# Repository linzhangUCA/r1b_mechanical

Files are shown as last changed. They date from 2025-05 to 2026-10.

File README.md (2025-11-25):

# R1Bot's Mechanical Design

## Preview
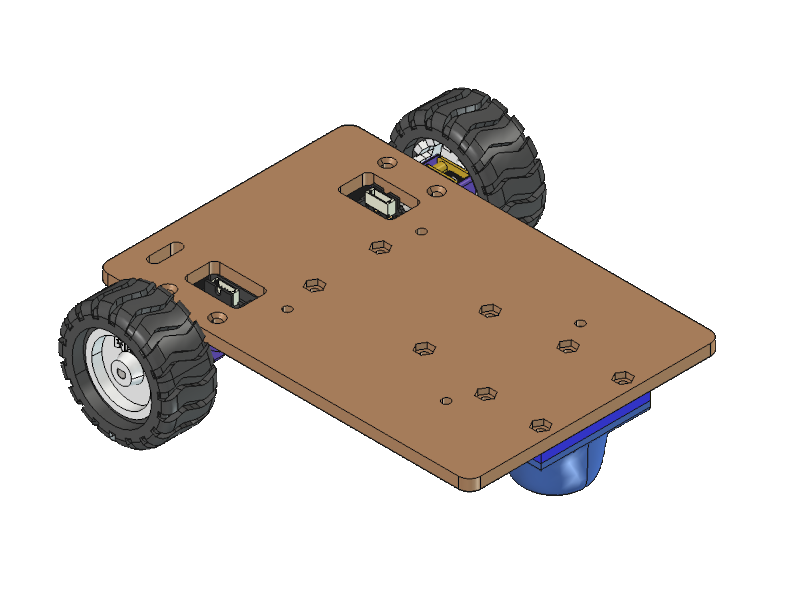
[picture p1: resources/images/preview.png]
preview


## Assembly Parts List
| Name | Description | Quantity |
| :--- | :--- | ---: |
| [Base plate](/prints/STL/Base.stl) | holds all components | 1 |
| [Motor Bracket](/prints/STL/MotorBracket.stl) | holds motor on base | 2 |
| [Caster Wheel](/prints/STL/CasterWheel.stl) | offers omni-directional rotate | 1 |
| M2.5x14 flathead screw | secures caster wheel on base  | 4 |
| [Tire](/prints/STL/Tire.stl) | provides traction | 2 |
| [Wheel](/prints/STL/Wheel.stl) | attaches to motor and supports tire | 2 |
| [N20 geared DC motor with encoder](https://www.robotshop.com/products/e-s-motor-6v-1001-micro-metal-gearmotor-w-encoder-cable-150rpm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) | spins and senses wheel | 2 |
| M2.5x8 flathead screw | secures motor bracket on base  | 4 |
| [Battery holder](https://a.co/d/j4Nehb4) | hosts 2 Li-ion batteries  | 1 |
| 18650 Lithium-ion Battery | provides DC power | 2 |
| M2.5x5 flathead screw | secures battery holder on base  | 4 |
| M2.5 nut | pairs with the screws  | 16 |
| [Power expansion board](https://category.yahboom.net/collections/rp-power/products/power-board-pi5) (PEB) | regulates 6~24 V to 5 V  | 1 |
| M2.5x10 standoff | supports PEB | 4 |
| [Motor control board](https://github.com/linzhangUCA/r1b_electrical) (MCB) | bridges Pico, Pololu713, HC-SR04, motors and encoders  | 1 |
| M2.5x15 standoff | supports MCB | 4 |
| M2.5x6 screw | caps MCB | 4 |

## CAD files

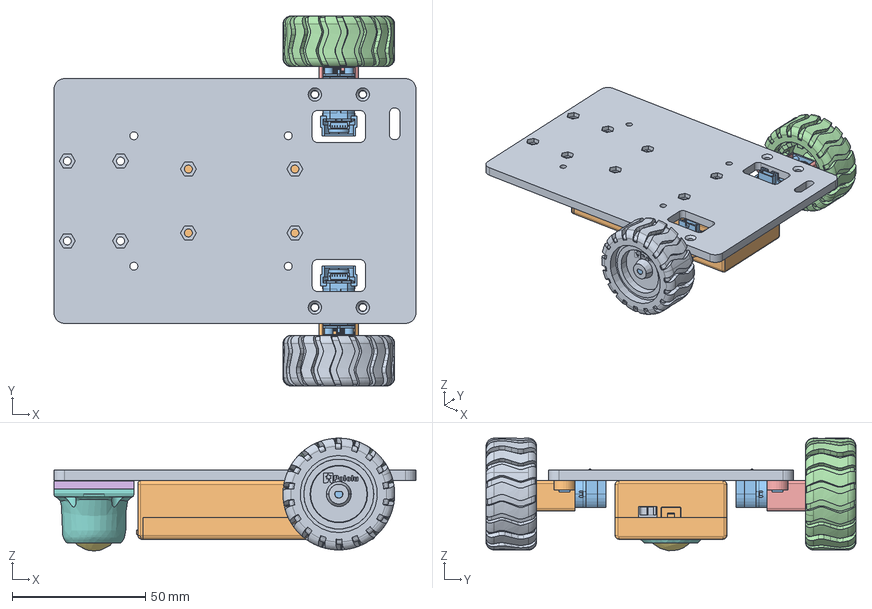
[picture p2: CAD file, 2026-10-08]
tbot_assembly.FCStd
136.0 x 139.0 x 42.3 mm
base_link
Case, 3.7V 2X 18650 Battery Holder with On Off Switch
Switch and Wiring Cover, 3.7V 2X 18650 Battery Holder with On Off Switch
Battery Conduction Clip, 3.7V 2X 18650 Battery Holder with On Off Switch
Spring, 3.7V 2X 18650 Battery Holder with On Off Switch
Battery Conduction Clip, Positive Terminal, 3.7V 2X 18650 Battery Holder with On Off Switch
Battery Conduction Clip, Negative Terminal, 3.7V 2X 18650 Battery Holder with On Off Switch
Spring, 3.7V 2X 18650 Battery Holder with On Off Switch001
Slide Switch SPDT, 3.7V 2X 18650 Battery Holder with On Off Switch_OFF
Cover, 3.7V 2X 18650 Battery Holder with On Off Switch
left_Pololu_motor
left_wheel
left_motor_backet
LiftPad
Roller_Sphere
Roller_Housing
right_wheel
right_motor_backet
right_Pololu_motor

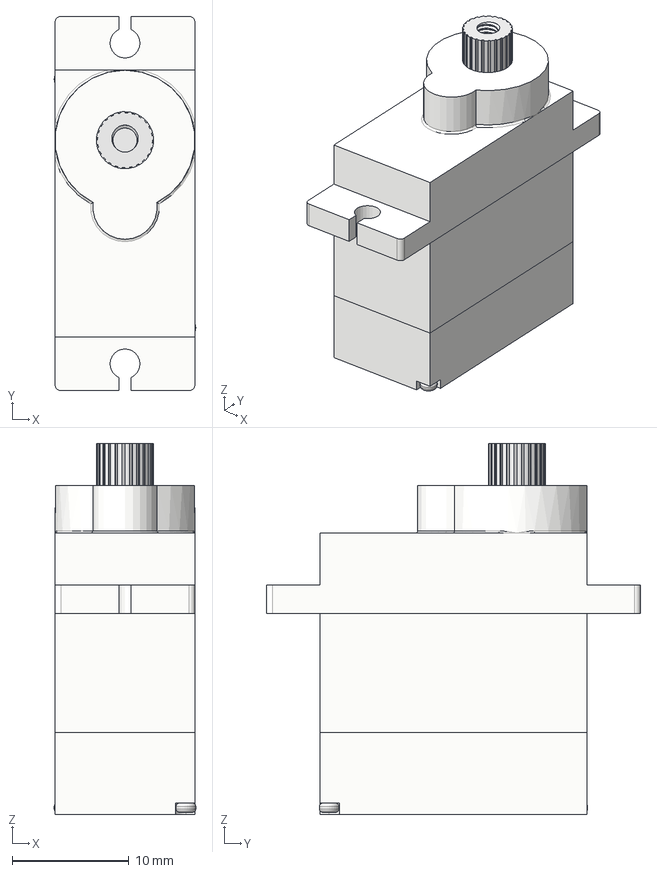
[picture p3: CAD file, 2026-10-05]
resources/steps/Assembly Micro Servo MG90S.step
12.1 x 32.1 x 31.8 mm
Micro Motor
Middel Part
Buttom Part
Shaft B
Gear C
Gear B
Gear A
Main Shaft with Gear
Upper Part
Main Screw x 2

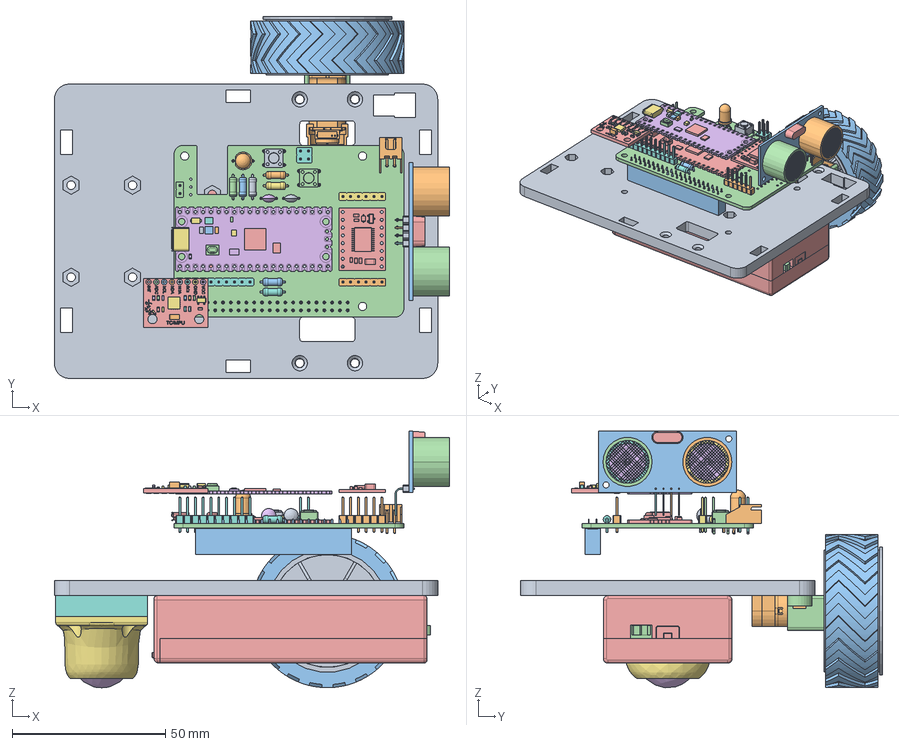
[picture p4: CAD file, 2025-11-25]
RobotAssembly.FCStd
128.9 x 118.0 x 83.6 mm
Wheel
Motor
Tire
MotorBacket
Case, 3.7V 2X 18650 Battery Holder with On Off Switch
Switch and Wiring Cover, 3.7V 2X 18650 Battery Holder with On Off Switch
Battery Conduction Clip, 3.7V 2X 18650 Battery Holder with On Off Switch
Spring, 3.7V 2X 18650 Battery Holder with On Off Switch
Battery Conduction Clip, Positive Terminal, 3.7V 2X 18650 Battery Holder with On Off Switch
Battery Conduction Clip, Negative Terminal, 3.7V 2X 18650 Battery Holder with On Off Switch
Spring, 3.7V 2X 18650 Battery Holder with On Off Switch001
Slide Switch SPDT, 3.7V 2X 18650 Battery Holder with On Off Switch_OFF
Cover, 3.7V 2X 18650 Battery Holder with On Off Switch
Roller_Sphere
Roller_Housing
LiftPad
Base
JST_XH_S2B-XH-A_1x02_P2.50mm_Horizontal
R_Axial_DIN0207_L6.3mm_D2.5mm_P7.62mm_Horizontal
R_Axial_DIN0207_L6.3mm_D2.5mm_P7.62mm_Horizontal001
HC-SR04
HC-SR005
HC-SR006
HC-SR007
HC-SR008
HC-SR009
HC-SR010
HC-SR011
HC-SR012
HC-SR013
HC-SR014
HC-SR015
HC-SR016
HC-SR017
HC-SR018
PinHeader_1x02_P2.54mm_Vertical
tb6612fng-dual-motor-driver-carrier
C_Disc_D4.7mm_W2.5mm_P5.00mm
PinHeader_1x06_P2.54mm_Vertical
R_Axial_DIN0207_L6.3mm_D2.5mm_P7.62mm_Horizontal002
R_Axial_DIN0207_L6.3mm_D2.5mm_P7.62mm_Horizontal003
PinHeader_1x06_P2.54mm_Vertical001
R_Axial_DIN0207_L6.3mm_D2.5mm_P7.62mm_Horizontal004
SW_PUSH_6mm
RaspberryPi_Pico_Module_KiCad
PICO_REF_BOARD
PICO_REF_USB
PICO_REF_USB001
PICO_REF_USB002
PICO_REF_USB003
PICO_REF_USB004
PICO_REF_SWITCH
PICO_REF_MICROCONTROLLER
PICO_REF_LED
PICO_REF_COMP_1
PICO_REF_COMP_2
PICO_REF_COMP_3
PICO_REF_COMP_004
PICO_REF_COMP_4
PICO_REF_COMP_5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

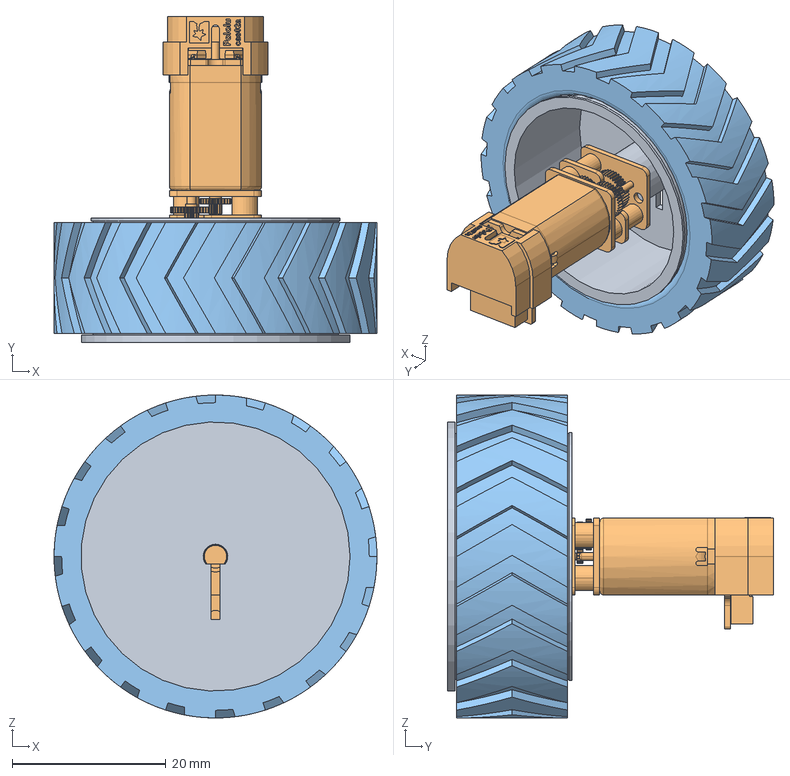
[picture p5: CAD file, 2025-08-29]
wheel_assembly.FCStd
42.0 x 42.4 x 42.0 mm
Rim
customer_step_mmgm_cas02_enc03d_2
Tire

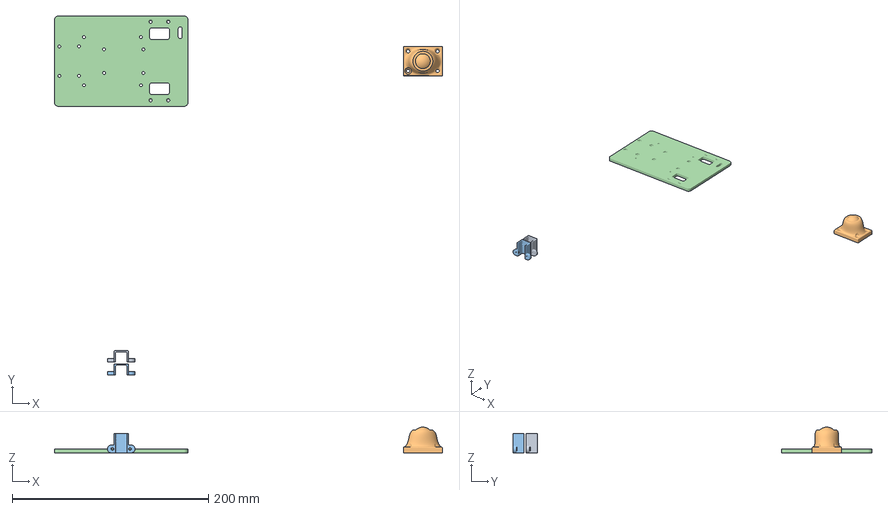
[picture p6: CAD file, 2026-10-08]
prints/3MF/tbot_prototype_split.3mf
395.2 x 365.6 x 26.3 mm
MotorBacket.step x 2
ShortCasterWheel.step
tbot_assembly-base_link.step

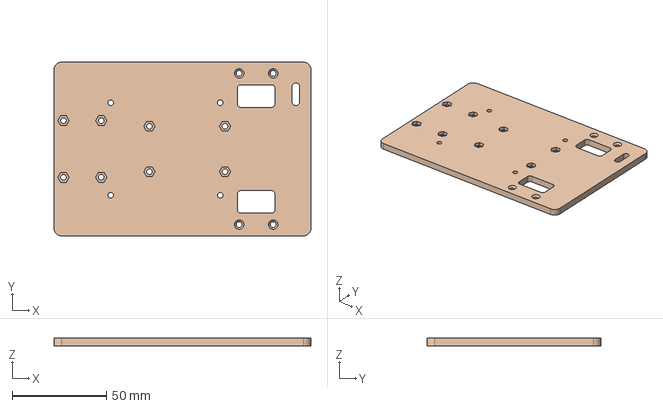
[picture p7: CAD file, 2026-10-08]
prints/STEP/BaseLink.step
136.0 x 92.0 x 4.00 mm

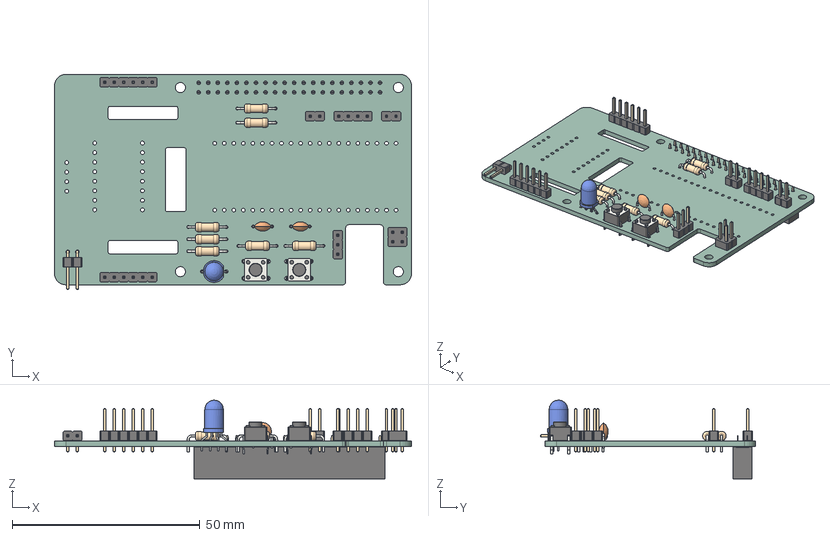
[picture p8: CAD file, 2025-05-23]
resources/circuit_boards/cerebellum.step
95.0 x 57.3 x 21.0 mm
PinHeader_1x04_P2.54mm_Vertical
R_Axial_DIN0207_L6.3mm_D2.5mm_P10.16mm_Horizontal x 7
PinHeader_1x02_P2.54mm_Vertical x 2
SW_PUSH_6mm_H5mm x 2
C_Disc_D4.7mm_W2.5mm_P5.00mm x 2
PinHeader_2x02_P2.54mm_Vertical
LED_D5.0mm-4_RGB_Wide_Pins
PinHeader_1x06_P2.54mm_Vertical x 2
PinHeader_1x02_P2.54mm_Horizontal
PinHeader_1x03_P2.54mm_Vertical
PinSocket_2x20_P2.54mm_Vertical
cerebellum_PCB

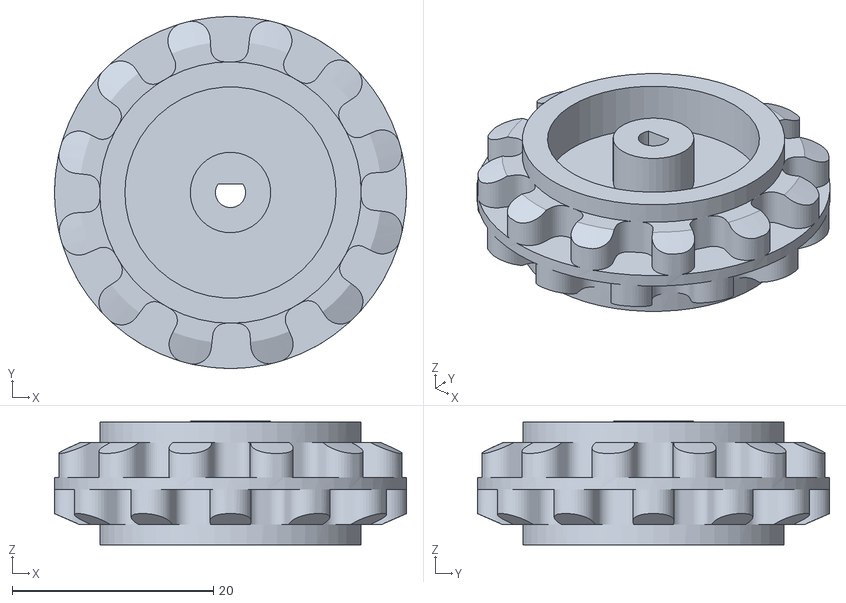
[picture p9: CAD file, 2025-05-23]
resources/drivetrain/Pololu_wheel_with_motor_shaft.STL
35.0 x 35.0 x 12.3

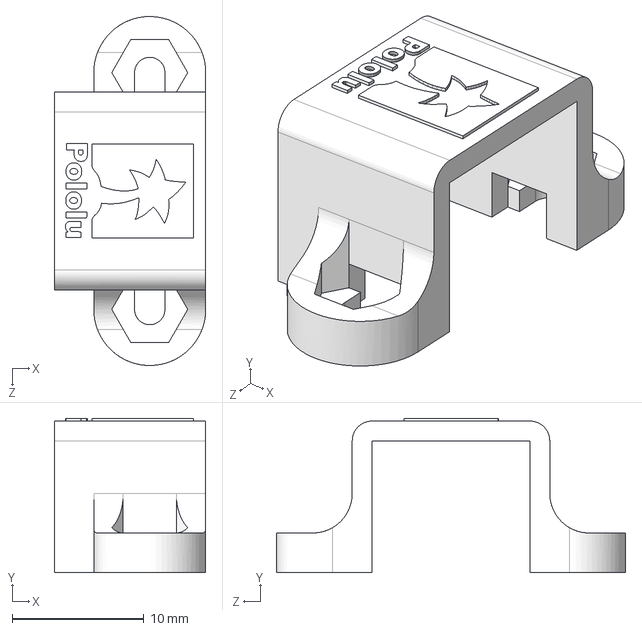
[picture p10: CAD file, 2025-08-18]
resources/drivetrain/resources/motor-bracket.step
11.5 x 11.7 x 26.5 mm

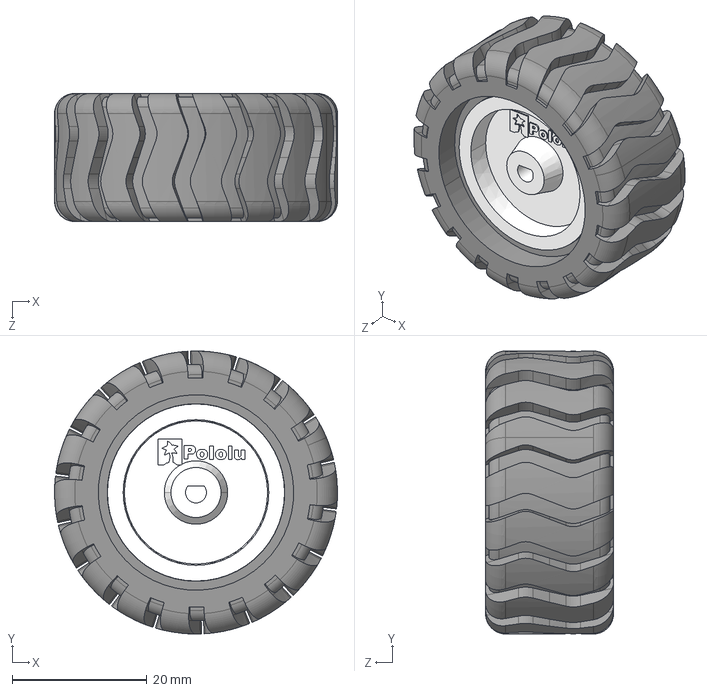
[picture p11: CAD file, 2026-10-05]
resources/steps/pololu-wheel-42x19mm.step
42.0 x 42.0 x 19.0 mm

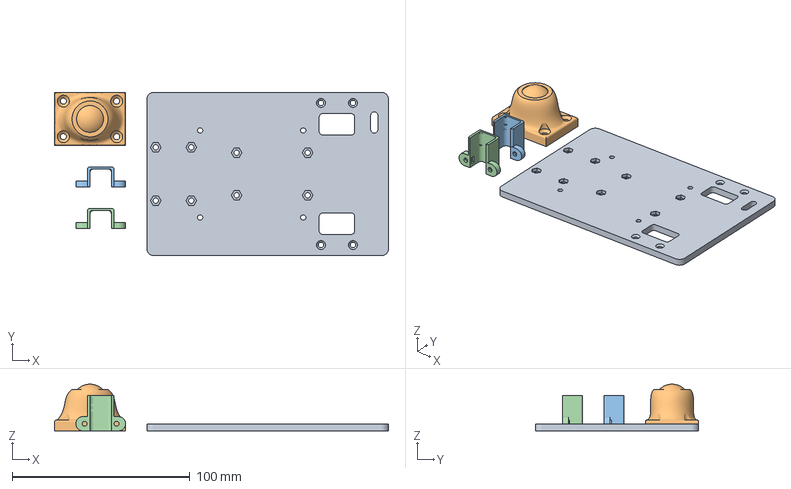
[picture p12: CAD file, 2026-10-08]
prints/3MF/tbot_prototype_all.3mf
188.0 x 92.0 x 26.3 mm
tbot_assembly-base_link.step
ShortCasterWheel.step
MotorBacket.step x 2

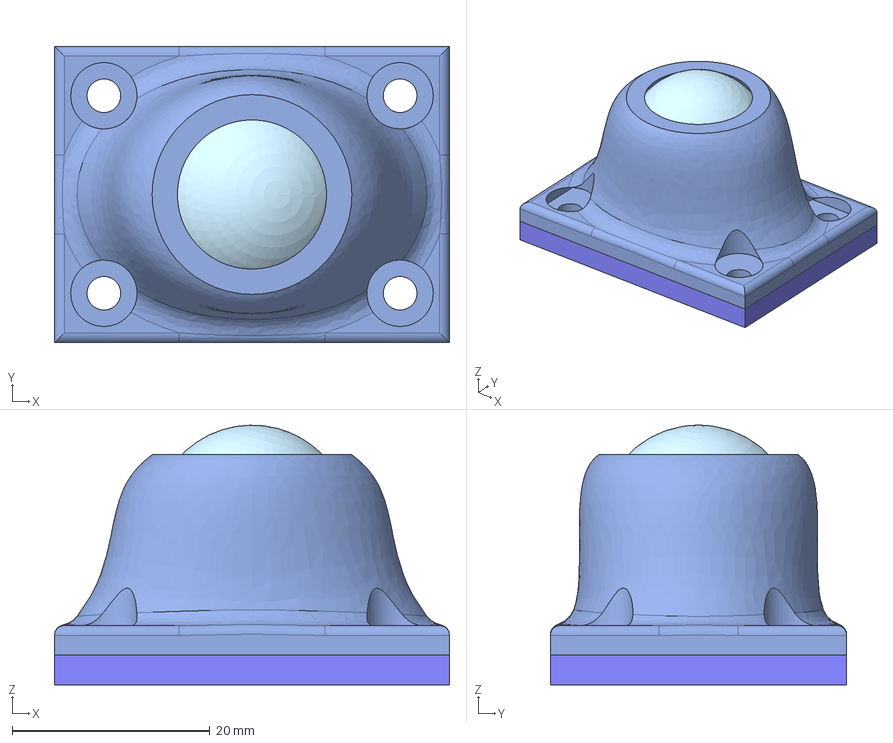
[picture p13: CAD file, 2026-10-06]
prints/STEP/ShortCasterWheel.step
40.0 x 30.0 x 26.3 mm
LiftPad
Roller_Sphere
Roller_Housing

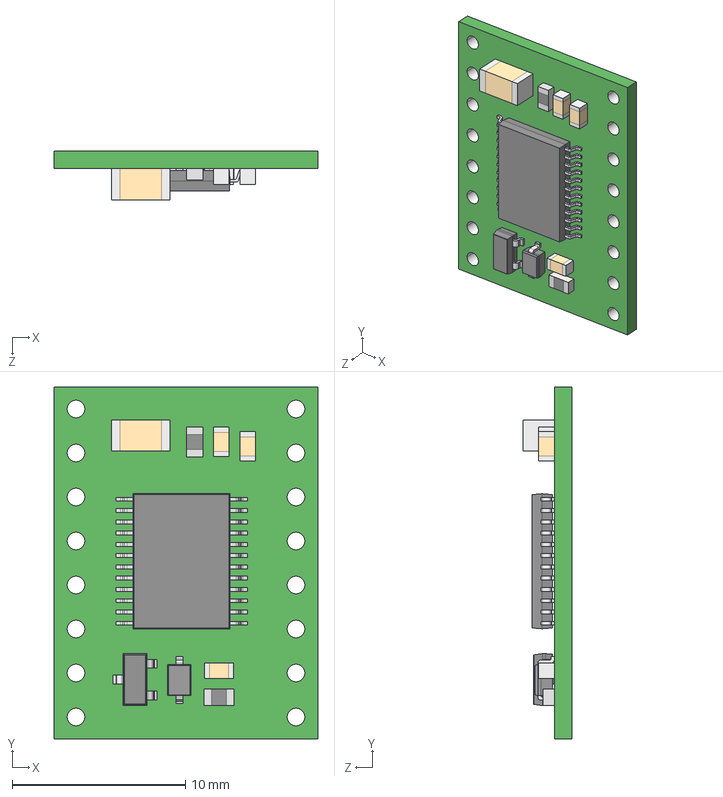
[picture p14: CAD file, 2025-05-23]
resources/circuit_boards/tb6612fng-dual-motor-driver-carrier.step
15.2 x 20.3 x 2.82 mm

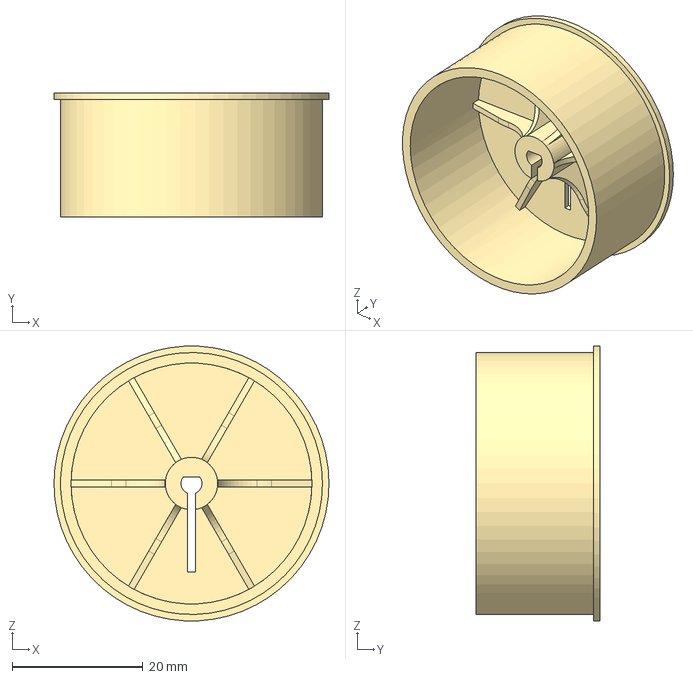
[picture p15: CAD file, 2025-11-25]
prints/STEP/Wheel.step
42.0 x 19.0 x 41.9 mm

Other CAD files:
resources/circuit_boards/Pico.step
resources/steps/N20Encoder.step
WA-Tire.stl
prints/STEP/Tire.step
WA-Rim.stl
motor_bracket.FCStd
prints/STEP/CasterWheel.step
prints/STEP/MotorBacket.step
resources/RollerMod2026.FCStd
resources/battery/18650_spacer.stl
resources/steps/RollerMod2026.step
resources/steps/gy521.step

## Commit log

2025-05-20 import lidar and motor models
2025-05-20 add battery to part list
2025-05-21 import pcb model
2025-05-22 import sonar model
2025-05-22 unite circuit boards
2025-05-22 import driving wheels
2025-05-23 reorganize external resources
    [18650_spacer.stl, Pico.step, Pololu_wheel_with_motor_shaft.STL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]
2025-05-23 finish drivetrain import
    [cerebellum.step]
2025-08-18 start motor bracket design
    [motor-bracket.step, motor_bracket.FCStd]
2025-08-18 reduce screw holder size
    [motor_bracket.step]
2025-08-19 shorten screw holder
    [motor_bracket.step]
2025-08-19 wheel design v1 finish
    [wheel.FCStd, wheel.step]
2025-08-19 tighten motor hole
    [wheel.FCStd, wheel.step]
2025-08-19 add tire design
    [wheel-Rim.step, wheel-Tire.step, wheel.FCStd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]
2025-08-19 save changes
    [wheel.FCStd]
2025-08-20 export wheel assembly
    [Wheel-Assembly.step]
2025-08-20 update motor bracket design
    [motor_bracket.step]
2025-08-20 update motor bracket
    1. increase screw pocket size
    2. add a window for easier inserting screw
    [motor_bracket.FCStd, motor_bracket.step]
2025-08-20 update rim design
    shorten inner teeth width
    [wheel-Rim.step, wheel.FCStd]
2025-08-20 update tire design- increase inner ring and rim groove size
    [wheel-Tire.step, wheel.FCStd]
2025-08-20 update wheel design
    1. Make tire easier to install
    2. increase rim mounting width
    [Wheel-Assembly.step, wheel-Rim.step, wheel-Tire.step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]
2025-08-26 add new design of wheel assembly
    [WA-Rim.stl, WA-Tire.step, WA-Tire.stl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]
2025-08-26 fix tire size
    [WA-Tire.stl, wheel_assembly.FCStd]
2025-08-26 reduce rim outer ring size
    [WA-Rim.stl, wheel_assembly.FCStd]
2025-08-26 enlarge rim's pocket for motor
    [WA-Rim.stl, wheel_assembly.FCStd]
2025-08-26 tighten gap between rim and tire
    [WA-Rim.stl, WA-Tire.stl, wheel_assembly.FCStd]
2025-08-27 forget about past
    [WA-Rim.stl, WA-Tire.step, WA-Tire.stl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]
2025-08-27 initiate new wheel assembly design
    [wheel.FCStd, wheel_assembly.FCStd]
2025-08-28 finish tire design
    [wheel_assembly.FCStd]
2025-08-28 update design
    [WA-Rim.stl, WA-Tire.stl, Wheel_Assembly.stl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]
2025-08-29 update tire design
    trimmed tire surface
    [WA-Tire.stl, wheel_assembly.FCStd]
2025-08-29 add fillet to tire inner ring
    [WA-Tire.stl, wheel_assembly.FCStd]
2025-10-12 Revert "deepen bedtop screw pockets to fit m2.5-12 screws"
    This reverts commit 99433a11019f29b00e18a5fe08b4db0f39726d0b.
    [Base.step, RobotAssembly.FCStd]
2025-10-16 add a platform on top
    [MiniBBPlat.step, RobotAssembly.FCStd]
2025-11-24 update base design to adapt motor control pcb
    [Base.step, RobotAssembly.FCStd, gy521.step]
2025-11-25 update printables
    [Base.step, CasterWheel.step, MiniBBPlat.step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]
2025-11-25 update base step
    [Base.step]
2025-11-25 update README with parts list
    [Base.step, Base.stl, CasterWheel.step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]
